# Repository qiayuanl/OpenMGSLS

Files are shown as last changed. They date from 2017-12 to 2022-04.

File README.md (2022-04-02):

# OpenMGSLS
**This project was developed in high school, is very naive and low reference value, please refer to it with caution!**

A brief Introduction and demo video show in [my webstie](https://qiayuanliao.netlify.app/project/sls/) 

## Introduction
There have many 3D printing technologies, many of them use the laser to process materials like SLS(Selective Laser Sintering). Move the laser quickly and accurately became an important thing in the 3D printing. Laser galvanometer which widely used in industrial marking has the many advan- tages such as high-speed and high-precision.So this project tries to develop a system which can use laser galvanometer in 3D printing.
## methord
Laser galvanometer works the same as the voltmeter, the volt determines the angle of mirrors which reflect the laser. We use serial to communicate with the computer and receive the GCode(GCode is most widely used nu- merical control programming language), process the GCode and plan, cal- culate the mirrors angle for each movement, use SPI to send the volt data to the DAC module, output the volt and make galvanometer turn to the corresponding angle.Then this poject develop a desktop SLS 3D printer to test the control system.
## date
The galvanometer control system and 3D printer developed in this project are compatible with most 3D printing slicing software(like simplify3D Cura), the laser point movement speed can reach 2,000mm/s, the print accuracy can reach 0.01mm and it can print many complex structures without sup- ports.
## summary
This project develops a system which can use the GCode to control the galvanometer and build a desktop SLS 3D printer base on this system. Rely on this system the printer can do 3D printing faster and more accurately than most of another desktop 3D printer.

## 引言
现存的 3D 打印技术中许多使用激光来加工材料，快速且精确地移动激光非常重要。激光振镜广泛应用于工业打标，具有高速、高精度的优点。本项 目是开发了一套可以在选择性激光烧结 3D 打印机上使用激光振镜的系统。

## 方法
激光振镜的工作原理与电压表相同，电压决定偏转激光的反射镜的角度。 这个项目使用串又与计算机通讯并接收 G代码(G 代码是使用最广泛的数 控编程语言)，对其进行处理规划，计算每个运动对应的电压，使用SPI将数据输出到DAC模块，输出电压，使振镜转到相应的角度。后另外开发了一台选择性激光烧结3D打印机来实验开发的控制系统。

## 数据
这个项目开发的振镜控制系统及3D打印机可以兼容大多数3D打印切片软件如:Simplify3D、Cura。激光点移动速度可以达到 2,000mm/s，打印精度可以达到0.01mm。

## 总结
这个项目开发了一个可以使用 GCode 来控制振镜的系统, 并在此基础上开发了一台桌面级选择性激光烧结3D打印机，可以比其他大多数桌面3D打印机更快，更准确地进行 3D 打印。



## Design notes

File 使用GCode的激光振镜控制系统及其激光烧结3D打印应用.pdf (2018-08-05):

# 使⽤ GCode 的激光振镜控制系统及其激光烧 结 3D 打印应⽤

### 廖洽源

⾼三级

### 潮州市⾦⼭中学 March 27, 2018

Abstract

现存的 3D 打印技术中许多使⽤激光来加⼯材料，快速且精确地移动激 光⾮常重要。激光振镜⼴泛应⽤于⼯业打标，具有⾼速、⾼精度的优点。本项 ⽬是开发了⼀套可以在选择性激光烧结 3D 打印机上使⽤激光振镜的系统。 激光振镜的⼯作原理与电压表相同，电压决定偏转激光的反射镜的⾓度。 这个项⽬使⽤串⼜与计算机通讯并接收 G 代码（G 代码是使⽤最⼴泛的数 控编程语⾔），对其进⾏处理规划，计算每个运动对应的电压，使⽤ SPI 将 数据输出到 DAC 模块，输出电压，使振镜转到相应的⾓度。后另外开发了 ⼀台选择性激光烧结 3D 打印机来实验开发的控制系统。 这个项⽬开发的振镜控制系统及 3D 打印机可以兼容⼤多数 3D 打印切 ⽚软件如：Simplify3D、Cura。激光点移动速度可以达到 2,000mm/s，打印 精度可以达到 0.01mm。
这个项⽬开发了⼀个可以使⽤ GCode 来控制振镜的系统，并在此基础上 开发了⼀台桌⾯级选择性激光烧结 3D 打印机，可以⽐其他⼤多数桌⾯ 3D 打印机更快，更准确地进⾏ 3D 打印。

There have many 3D printing technologies, many of them use the laser to process materials like SLS(Selective Laser Sintering). Move the laser quickly and accurately became an important thing in the 3D printing. Laser galvanometer which widely used in industrial marking has the many advantages such as high-speed and high-precision.So this project tries to develop a system which can use laser galvanometer in 3D printing.
Laser galvanometer works the same as the voltmeter, the volt determines the angle of mirrors which reflect the laser. We use serial to communicate with the computer and receive the GCode(GCode is most widely used numerical control programming language), process the GCode and plan, calculate the mirrors angle for each movement, use SPI to send the volt data to the DAC module, output the volt and make galvanometer turn to the corresponding angle.Then this poject develop a desktop SLS 3D printer to test the control system.
The galvanometer control system and 3D printer developed in this project are compatible with most 3D printing slicing software(like simplify3D Cura), the laser point movement speed can reach 2,000mm/s, the print accuracy can reach 0.01mm and it can print many complex structures without supports.
This project develops a system which can use the GCode to control the galvanometer and build a desktop SLS 3D printer base on this system. Rely on this system the printer can do 3D printing faster and more accurately than most of another desktop 3D printer.

2

## Contents

1 前言 | 4
2 控制理论及实现 | 7
3 机械设计 | 10
4 结果 | 12
5 结论 | 13
6 致谢 | 13
7 参考文献 | 13

3

## 1 前言

### 1.1 激光打标

激光打标是使⽤激光束在各种不同的
物质表⾯打上永久的标记的过程的统称, 电
⼦元器件、集成电路 (IC)、五⾦制品等都
是⽤这种设备来为产品加上商标 (⼆维⽮
量图).

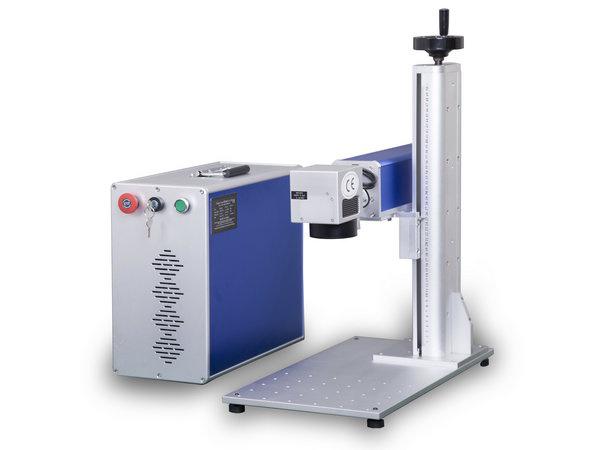
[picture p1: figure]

(a) 常见激光打标机

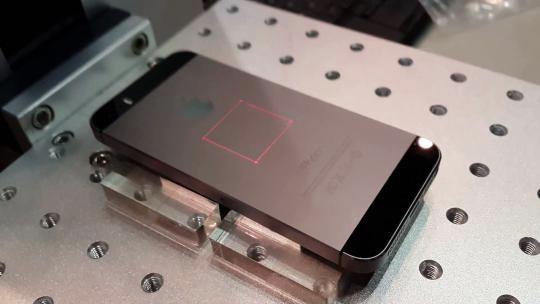
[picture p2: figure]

(b) iPhone ⼿机背⾯⽂字商标为激光打标制造

Figure 1: 激光打标

### 1.1.1 振镜电机

振镜是⼀种优良的⽮量扫描器件. 它是
⼀种特殊的摆动电机, 基本原理是通电线
圈在磁场中产⽣⼒矩, 但与旋转电机不同,
其转⼦上通过机械纽簧或电⼦的⽅法加有
复位⼒矩, ⼤⼩与转⼦偏离平衡位置的⾓
度成正⽐, 当线圈通以⼀定的电流⽽转⼦
发⽣偏转到⼀定的⾓度时, 电磁⼒矩与回
复⼒矩⼤⼩相等, 故不能象普通电机⼀样
旋转, 只能偏转, 偏转⾓与电流成正⽐, 与
电流计的原理相同, 故振镜又叫电流计扫
描器 (galvanometric scanner).

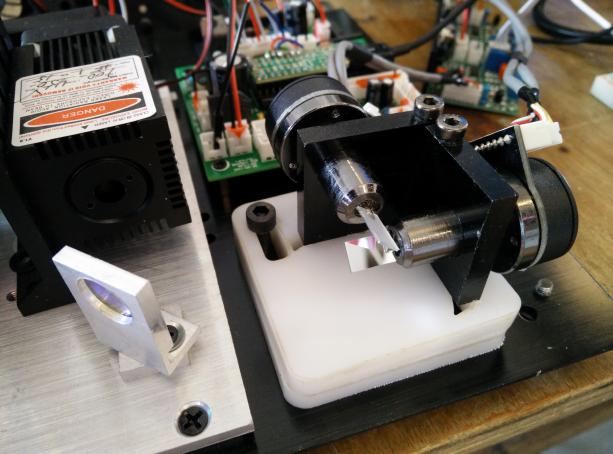
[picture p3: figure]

Figure 2: 两个振镜电机和激光器构成的
XY ⼆维扫描系统

### 1.2 3D 打印

3D 打印机又称三维打印机 (3DP), 是
⼀种累积制造技术, 即快速成形技术的⼀
种机器, 它是⼀种数字模型⽂件为基础, 运
⽤特殊蜡材、粉末状⾦属或塑料等可粘合
材料, 通过打印⼀层层的粘合材料来制造
三维的物体. 现阶段三维打印机被⽤来制
造产品. 3D 打印⽆需机械加⼯或模具, 就
能直接从计算机图形数据中⽣成任何形状
的物体, 从⽽极⼤地缩短了产品的⽣产周
期, 提⾼了⽣产率, 在⼯业 (制造业、航天科
技、医疗⾏业等) 及民⽤ (教育研究、⽣活
⽤品等) 领域有着许多应⽤.

1.2.1 3D 打印机原理概述

3D 打印的⼀般流程如下:

建模 3D 打印模型可以使⽤计算机辅助设
计软件 (SolidWorks、AutoCAD) 或三维扫 描仪⽣成. ⼿动搜集制作 3D 图像所需的⼏
何数据过程同雕塑等造型艺术类似. 通过
3D 扫描, 可以⽣成关于真实物体的形状、外
表等的电⼦数据并进⾏分析. 以 3D 扫描得
到的数据为基础, 就可以⽣成被扫描物体
的三维电脑模型. ⽆论使⽤哪种 3D 建模软
件, ⽣成的 3D 模型 (通常为.skp、.dae、.3ds 或其它格式) 都需要转换成.STL 或.OBJ 这
类以三⾓形作为 3D 模型的基本单元的格
式.

分层 把模型放在 XY 平⾯上,Z 轴对应的
就是模型⾼度. 把 XY 平⾯抬⾼⼀定⾼度
再与模型的表⾯相交, 就可以得到模型在
这个⾼度上层切⽚. 所谓的分层就是每隔
⼀定⾼度就⽤⼀个 XY 平⾯去和模型相交
作层切⽚, 全部切完后就可以得到模型在
每⼀个⾼度上的轮廓线. 分层本质上就是
⼀个把 3D 模型转化为⼀系列 2D 平⾯的
过程, ⾃此之后的所有操作就都是在 2D 图
形的基础上进⾏. 将 XY 平⾯与构成模型
的三⾓⾯进⾏相交, ⼀个平⾯和⼀个三⾓
形相交, 就得到⼀条线段. 将这些线段连起
来就能得到某 Z 轴⾼度的 XY 轴外形轮廓.
改变 z 轴⾼度便能得到不同层的外形轮廓.

路径及 GCode 生成 得到外形轮廓后通
过算法⽣成填充路径后将路径转换成数控
程序 (铣床车床钻床等) 通⽤的 G 代码.

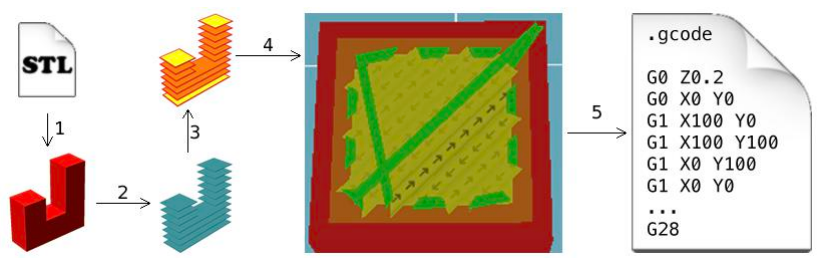
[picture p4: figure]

Figure 3: 电脑上的处理过程

### 1.2.2 常见 3D 打印机成型原理细分

在 20 世纪 70 年代后期, 出现了许多不
同的 3D 打印⽅法, 主要有三种熔融沉积成
型 (FDM)、⽴体光刻技术 (SLA)、选择性
激光烧结术 (SLS)

熔融沉积成型 (Fused deposition modeling, FDM) 是⼀种将各种热熔性的丝状
材料 (ABS 和 PLA 等) 加热熔化成形的⽅
法. 又可被称为 FFM 熔丝成型 (Fused Filament Modeling) 或 FFF 熔丝制造 (Fused Filament Fabrication), 其后两个不同名词 主要只是为了避开前者 FDM 专利问题,
然⽽核⼼技术原理与应⽤其实均是相同的.
材料被加热到半液体状态后, 在 GCode 的
控制下,FDM 装置的喷嘴就会沿着模型图
的表⾯移动, 将热塑性材料挤压出来, 在
该层中凝固形成轮廓.FDM 装置会使⽤两
种材料来执⾏打印的⼯作, 分别是⽤于构
成成品的建模材料和⽤作⽀架的⽀撑材料,

透过喷嘴垂直升降, 材料层层堆积凝固后,
就能由下⽽上形成⼀个 3D 打印模型的实
体. 打印完成实体.
(a) 1 为喷头 2 为打印半完成的零件 3 为底板

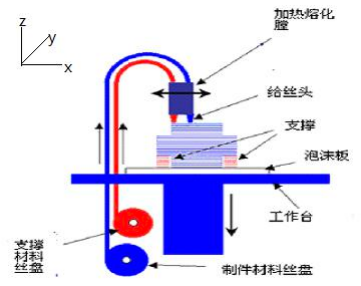
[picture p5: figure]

(b) 另⼀个视⾓

Figure 4: FDM3D 打印原理

优点 在 3D 打印技术中,FDM 的机械
结构最简单, 设计也最容易, 制造成本、维
护成本和材料成本也最低, 因此桌⾯级 3D
打印机中⼤部分使⽤的是这种技术.

缺点 难以精确控制出料形态与成型
效果, 同时温度对于 FDM 成型效果影响
⾮常⼤, ⽽桌⾯级 FDM 3D 打印机通常
都缺乏恒温设备, 因此基于 FDM 的桌⾯
级 3D 打印机的成品精度通常为 0.3mm-0.2mm 成品效果依然不够稳定, 在打印悬
空结构时还必须从⼀开始便构建“⽀撑”, 导
致精度进⼀步降低. 此外, 所以在对精度要
求较⾼的快速成型领域较少采⽤ FDM.

(a) 不打印⽀撑时对模型的要求

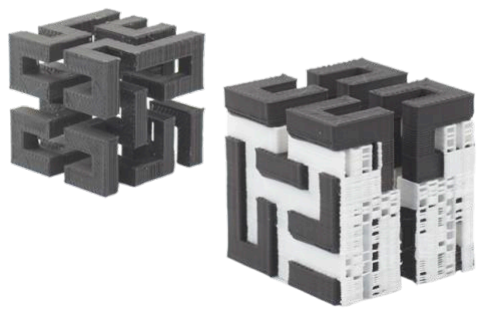
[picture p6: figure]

(b) ⽀撑去除前后对⽐ (⽩⾊为⽀撑)

Figure 5: FDM 对于零件的要求

选择性激光烧结 (Selective Laser Sintering,SLS) 选择性激光烧结使⽤激光将
粉末材料层熔化和固化成成品, 当激光打
到粉末上, 粉末会融化并且和附近粉末粘
在⼀起, 当激光在粉末层上匀速扫过⼀条
直线时, 粉末便会固化成⼀条细丝, 激光不
断扫描出⾯时, 粉末便可以被固化成⾯, 在
形成的⾯上⾯再铺⼀层粉末, 激光继续扫
描, 不断重复这个过程, 就能得到⼀个 3D
零件.

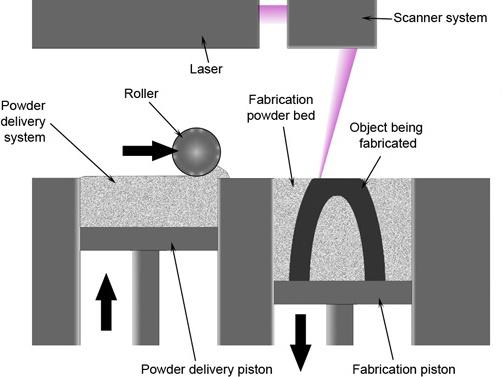
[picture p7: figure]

Figure 6: SLS3D 打印原理

优点 SLS 主要⽤于⼯业 3D 打印应⽤,
激光烧结技术可以使⽤⾮常多的粉末材料,
并制成相应材质的成品 SLS ⼴泛⽤于⽣产
功能原型和零件以及⼀些最终产品. 激光
烧结的最⼤优点是⼏乎完全的设计⾃由度;
过量的未熔化粉末在其⽣产时⽤作结构的
⽀撑, 这允许制造复杂的结构, ⽽不需要像
FDM SLA DLP 等构建额外的⽀撑.

缺点 技术⼗分复杂, 需要较⼤功率激
光, 桌⾯级的 SLS3D 打印机只少量存在于
⾼校或团队.

### 1.3 同类项目

### 1.3.1 现存桌面级 SLS3D 打印机

现存的桌⾯级 SLS3D 打印机都是在 FDM
3D 打印机 (或者激光切割机) 基础上改装
⽽成,XY 轴都是使⽤步进电机 + 同步带或
丝杠的⽅式拖着激光器进⾏直线运动, 这
种机构的最⼤运动速度只能到达 200mm/s
左右.

OpenSLS 项目 由美国莱斯⼤学约旦⽶
勒⽣理系统和先进材料实验室开发. 这个
项⽬的研究的主要⽅向为粉末烧结材料, 是
⽤⼀台 CO2 切割机改装⽽成.

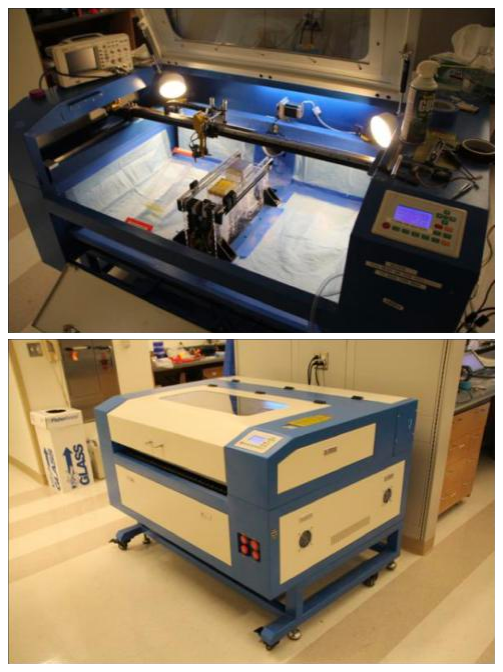
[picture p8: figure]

Figure 7: OpenSLS

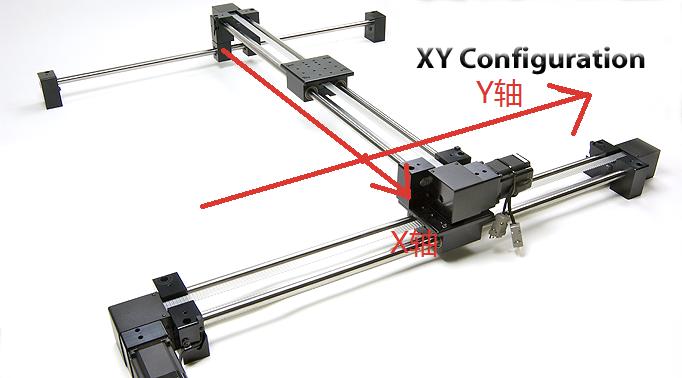
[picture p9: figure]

Figure 8: 步进电机直线模组

### 1.4 本项目简介

选题动机 步进电机直线模组的最⼤运动
速度只能到达 200mm/s 左右, 换⾔之, 激光 光斑的移动速度最⼤只有 200mm/s, ⽽激
光打标机的振镜电机进⾏扫描速度能达到
1000mms-5000mm/s, 是步进电机直线模组 的⼏⼗倍, 为什么不把激光打标机的执⾏
器 (两个振镜组成的振镜组) ⽤在 SLS3D
打印机上⾯??? 激光打标机使⽤的是⼆维
⽮量图不能适⽤于于 3D 打印, 所以开发⼀
个使⽤ Gcode 控制的振镜扫描系统是最佳
的选择.

目标 开发⼀个运⾏在 Arduino Due 单⽚
机上的控制程序及配套硬件, 可以⽤数控
设备通⽤的 G 代码控制振镜, 使得振镜兼
容常规切⽚软件, 可以⽤于 SLS3D 打印, 并
在此基础上研制使⽤振镜电机作为 XY 轴
的桌⾯级 SLS3D 打印机.

实现方法 在 PC 上使⽤切⽚软件将 3D
模型转换成 GCode, 每⾏ GCode 包含了
运动轨迹的信息, 将 GCode 通过串⼜发
送到 Arduino 控制器上,Arduino 控制器对 GCode 进⾏解释, 判断是否需要进⾏烧结
和移动粉缸和改变预热温度的操作及操作
数值, 对其进⾏进⼀步规划后执⾏, 后对
PC 进⾏应答⽽获取下⼀⾏ GCode, 不断
执⾏直⾄打印完成.

## 2 控制理论及实现

本章介绍本项⽬中振镜电机的控制及
补偿算法和步进电机加速度算法.

### 2.1 振镜扫描控制

### 2.1.1 单轴振镜电机直线扫描控制

条件 设⼀垂直于振镜旋转轴的直线及原
点, 反射镜⾯与直线夹⾓ π
4

, 运动⽬标点坐
标 x, 振镜中⼼与原点距离 d 且在原点正上
⽅, 反射镜偏⾓ α

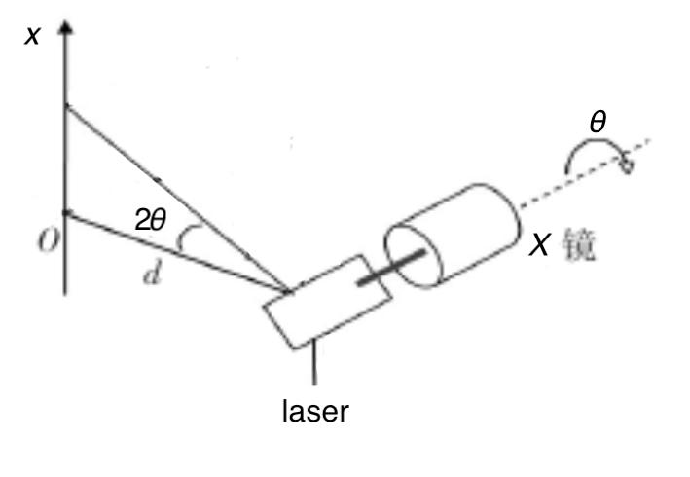
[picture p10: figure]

Figure 9: 单轴振镜电机⽰意图

正运动学:

x = d tan 2α | (1)

逆运动学:

α =

1
2

arctan

x
d

(2)

控制要求

输入: 运动⽬标点坐标 x

输出: 反射镜偏⾓ θ

控制函数 即逆运动学

f(x) = θ =

1
2

arctan

x
d

(3)

### 2.1.2 双轴振镜电机组平面扫描控制

条件 如果简单地使⽤单轴振镜电机的控
制⽅法

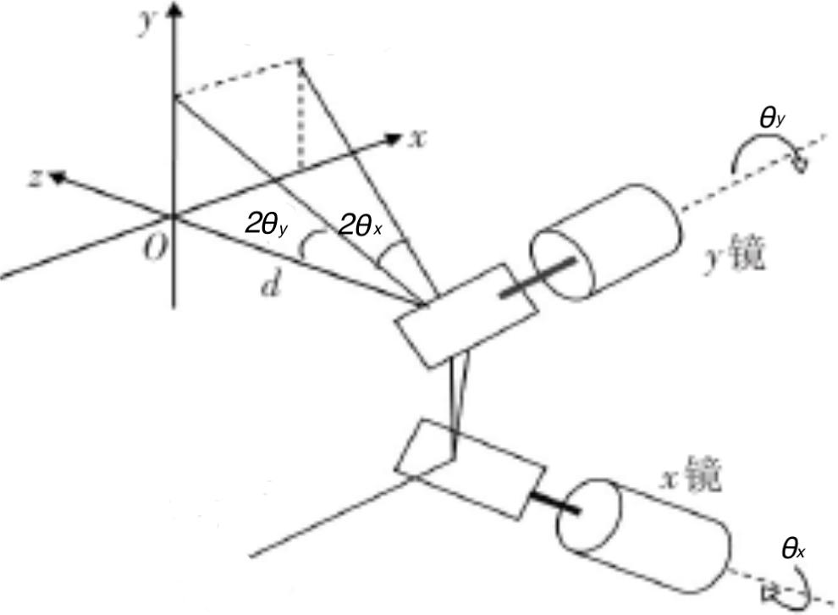
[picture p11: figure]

Figure 10: 双轴振镜电机组⽰意图

正运动学:
{
x = d tan 2θx
y = d tan 2θy

(4)

逆运动学:
{
2θx = arctan x
d
2θy = arctan y
d

(5)

控制要求

输入: 运动⽬标点坐标 (x, y)

输出: x 轴振镜反射镜偏⾓ θx , y 轴振
镜反射镜偏⾓ θy

控制函数
f(x, y) = {
θx =

1/2 arctan x
d
θy =

1/2 arctan y
d

(6)

但是如果使⽤这种控制⽅式,y 轴将会产⽣
枕型失真.

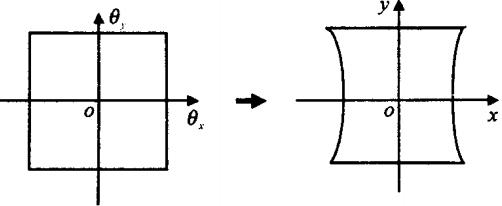
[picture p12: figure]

Figure 11: 扫描正⽅形图形的枕型失真

使⽤上述控制⽅式控制双轴的振镜组,
没有考虑到两个振镜的距离

条件 设 x 振镜和 y 振镜反射镜中轴之间
的距离为 e,y 振镜的轴线到扫描平⾯坐标
原点的距离为 d, 当 x,y 轴的光学偏转⾓分
别为 θx 和 θy 时, 扫描平⾯上相应激光斑坐
标为 (x, y), 当 θx = θy = 0 时,

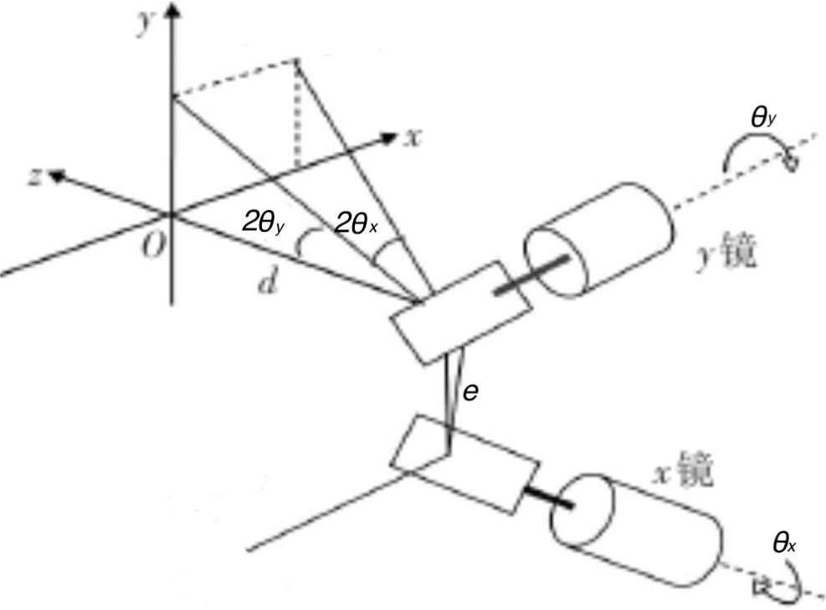
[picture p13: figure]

Figure 12: 双轴振镜电机组⽰意图

正运动学:
{
x = (e +

√
d

2 + y

2

)tan 2θx
y = d tan 2θy

(7)

逆运动学:

2θx = arctan x
e+

√
| d

2+y

2
2θy = arctan y
d

(8)

可见, 双轴振镜组的运动学模型是复杂的
⾮线性模型.

### 2.1.3 双轴振镜电机失真分析

失真产生 使⽤单轴扫描⽅式控制双轴振
镜组扫描垂直于 x 轴的直线时,θx 不变, 设
常数 c = 2 tan θx 由 (7) 可得

(x − ce)

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
= 1 | (9)

显然 (9) 描述的曲线为双曲线
定义 ε 为误差 x0 为预期位置 x 为实际位
置, 可见当 e 和 x0 越⼤时,x 轴偏移 ε 将越 ⼤

ε = x − x0 = (e +

√
d

2 + e

2

)tan 2θx (10)

验证 使⽤ Matlab 软件仿真扫描, 当 e = 5mm,d = 200mm 扫描长宽为 50mm 的正
⽅形图案

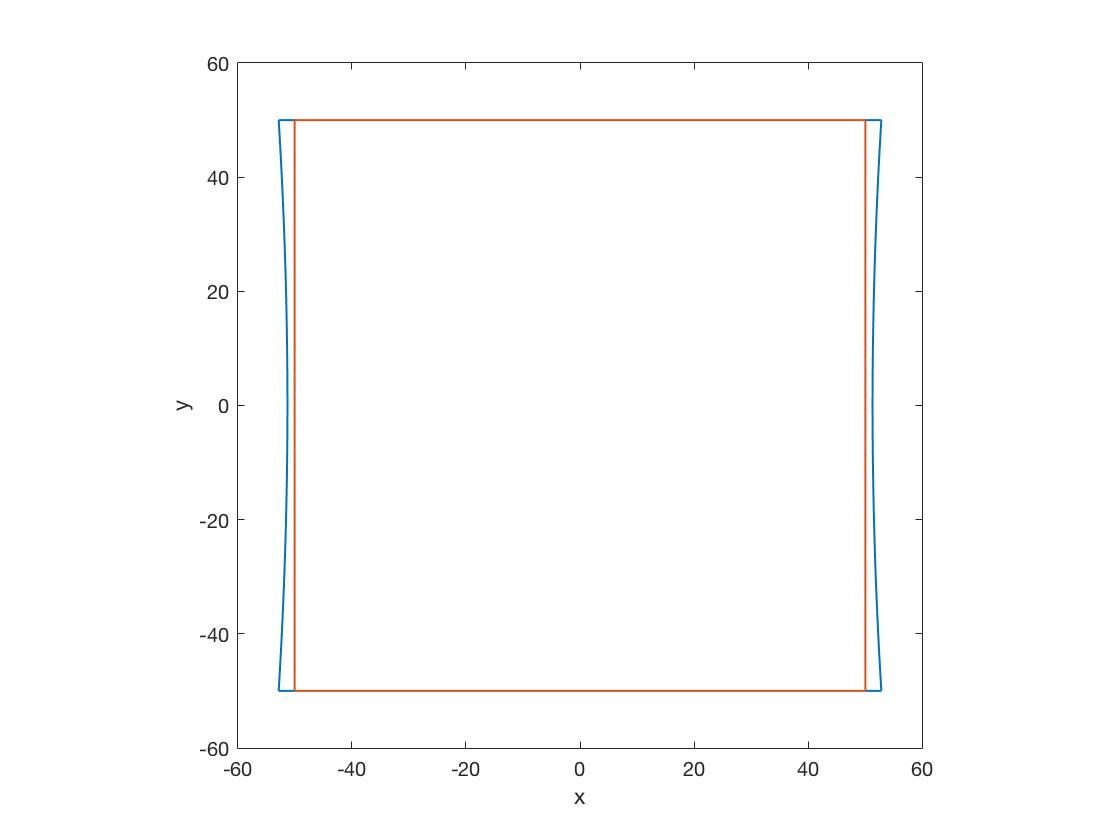
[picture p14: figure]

Figure 13: Matlab 仿真结果, 橙⾊为预期 图形, 蓝⾊为实际扫描图形

### 2.1.4 振镜控制实现

解释从串⼜接收的 G 代码缓存到队列
中, 空闲时间对其进⾏解析, 根据依据设

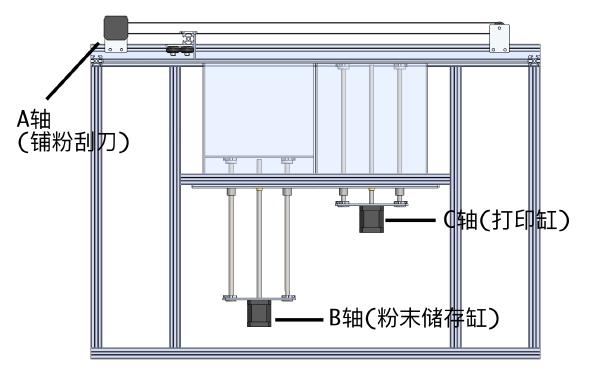
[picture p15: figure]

置的每秒插补次数对运动的路径进⾏分割，
对每个插补的 XY 轴分别计算⾓度, 后转换
成 DA 数值, 储存在两个队列中, 最后使⽤
定时器让振镜在某个细分时间点 pop 出队
列中的 DA 值, 通过 SPI 总线与 DAC8852(双 路) 以 50M 的速度进⾏通信, 将 DA 值
(DAC8552 为 16 位 0-5V 对应 0-65536) 发 送给 DAC 模块.

### 2.2 步进电机控制理论及实现

对于 SLS3D 打印机来说, ⼀共需要控
制 3 个轴:A 轴 (铺份刮⼑),B 轴 (粉末储存 缸),C 轴 (打印缸) 来完成铺粉过程
通过脉冲控制步进电机, 脉冲间隔决定电
机旋转速度, 需要考虑电机的加减速, 否则
电机将很容易失步

Figure 14: 三个直线运动轴

### 2.2.1 单轴步进电机加减速控制

条件 S 为加速距离 (单位:step), a 为加速 度 (单位:step/s
2

), v0 为初始速度 (单位:step/s),
v 为⽬标速度 (单位:step/s), t 为加速度时 间 (单位:s)

运动学

s =

v

2 − v

2
0
2a

(11)

v =

√
v

2
0 + 2aS | (12)

设 i 为第⼏步

vi =

√
v

2
i−1 + 2a | (13)

控制 使⽤定时器控制脉冲发送间隔设: Pi
为第 i 步的间隔时间 (单位:ticks) F 为定 时器唤醒周期 (单位 ticks/s)
Pi = F/vi | (14)

由 (13) 和 (14) 得:

Pi =

F
√

F
Pi−1

2
+ 2a

(15)

即

Pi =

Pi−1
√
1 + P

2
i−1

2a
F²

(16)

化简 泰勒展开在 −1 ≤ n ≤ 1 时
√

1
1+n ≈ 1 −

n

2 所以

Pi = Pi−1(1 −

P

2
i−1a
F²

) (17)

⽽ a F² 为常数

### 2.2.2 步进电机控制实现

在 (17) 中, ⽽ a F² 在加速度不变时为
常量, 在程序编译或者控制板开启时可以
预先计算在后⾯的运算中作为常量乘⼦参
与运算
设 R =
a

F² 则有
初始化:

P =

F
√
V

2
0 + 2a

(18)

加速时:
P = P(1 − RP²
) | (19)
到达⽬标速度时:
P = P | (20)

减速时:
P = P(1 + RP²
) | (21)
除了初始化, 其他计算只有乘法和加法, 因
此效率很⾼.
在控制板开启时初始化, 计算出第⼀次的
脉冲时间间隔, 设定定时器, 每次被定时器
唤醒就发送⼀个脉冲并计算下⼀个脉冲间
隔时间, 并根据计算出来的脉冲设定定时
器的唤醒间隔.

## 3 机械设计

本章介绍 SLS3D 打印机的机械结构都
使⽤ Solidworks 建模装配
⼀共开发了三代原型机, ⼀个实验平台, 将
着重介绍第三代. 细节详见公开的 solidworks 源⽂件

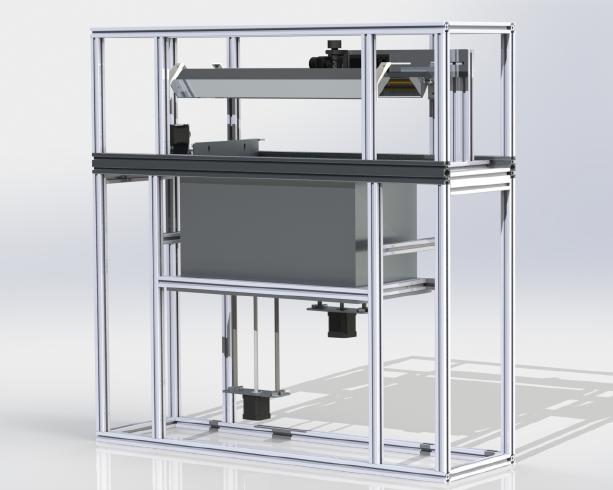
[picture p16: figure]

Figure 15: 第三代打印机渲染图

### 3.1 前代打印机

第一代 40WCO2 激光管激光振镜亚克⼒
及铝型材搭建的 Z 轴此版本的因为设计时
没有考虑到 CO2 激光功率过⼤，需要⽔冷，
亚克⼒不耐热等问题⽆法使⽤.

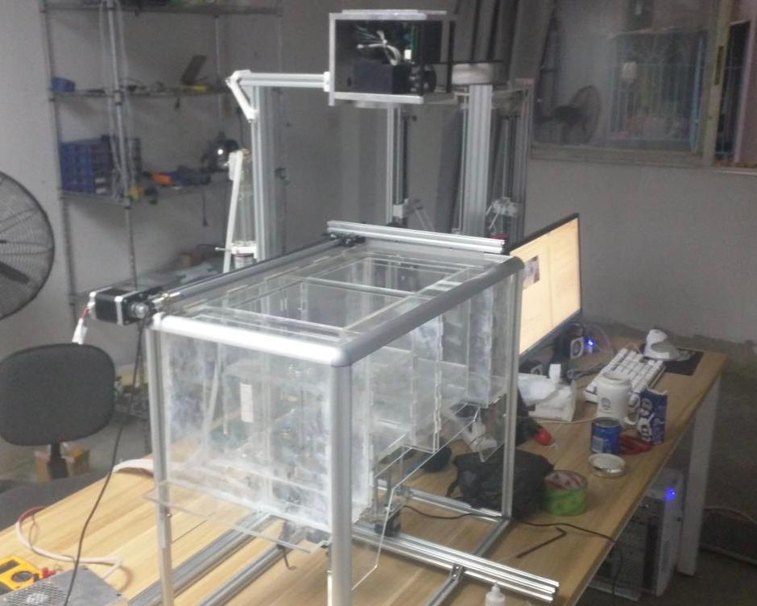
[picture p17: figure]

Figure 16: 第⼀代打印机实物图

第二代 使⽤半导体激光激光振镜铝板铝
型材搭建的第⼆代原型机

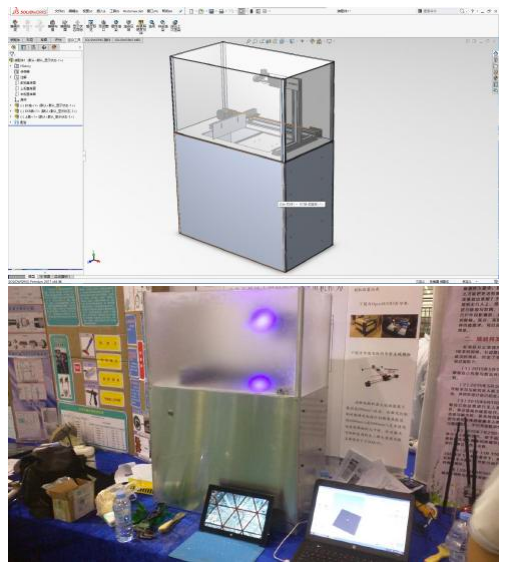
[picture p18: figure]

Figure 17: 第⼆代打印机渲染图及实物图

### 3.2 二维烧结实验平台

⼆维烧结实验平台⽤于单层烧结实验,
使⽤ 5W 半导体激光 (450nm) 及激光振镜, 并在底部加装加热板对粉末预热

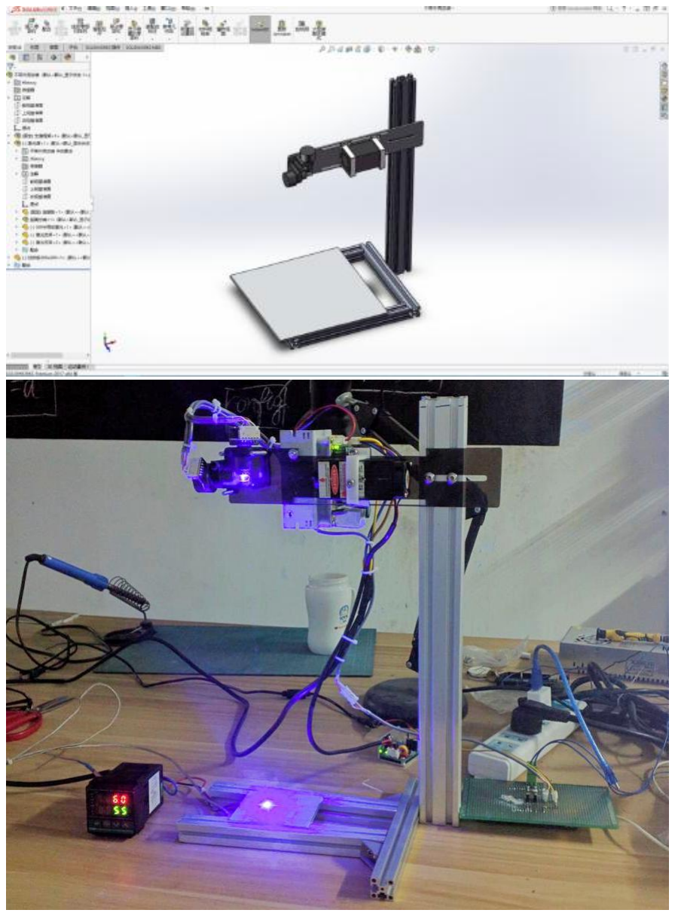
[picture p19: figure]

Figure 18: ⼆维烧结实验平台模型图及实
物图

### 3.3 第三代 SLS 打印机

打印机由三部分构成:
激光机构 (XY 轴)
粉末机构 (ABC 轴)
加热机构

激光机构 激光机构由两个振镜电机依照
上章所述的⽅式安装, 使⽤了⼀个 5W450nm
半导体激光器.

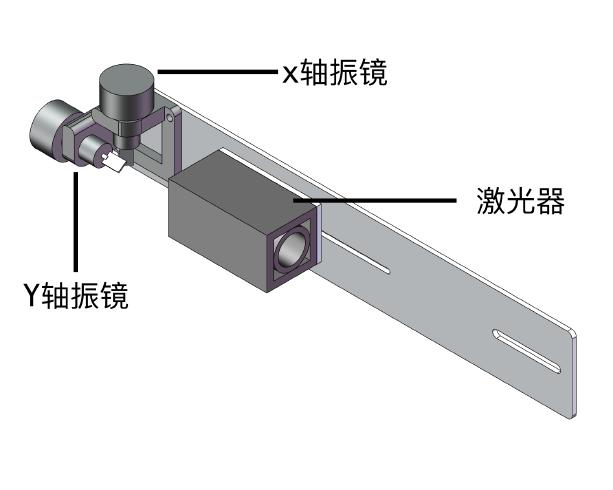
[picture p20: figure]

Figure 19: 激光机构

粉末机构 粉末机构的作⽤是覆盖⼀层粉
末到已烧结完成的打印件上⾯, 从⽽完成
整个三维堆积的过程
具体的过程如下:
初始状态时, 粉末储存缸 (B 轴) 的推杆降
到最低, ⽽打印缸推杆 (C 轴) 上升到距离
缸⼜极⼩的距离, 将两个缸都装满粉, 刮⼑
往返运动⼀次, 这时打印缸内便有了⼀层
薄⽽又均匀的粉末, 进⾏平⾯烧结后, 打印
缸下降⼀段距离, 粉末储存缸上升⼀段距
离, 这时便有部分粉末从粉末储存缸的缸
⼜溢出, 刮⼑往返⼀次, 将粉末储存缸的粉
末带到打印缸, 并铺匀, 这时, 第⼀次平⾯
烧结得到的打印件上⾯便覆盖了⼀层粉末,
继续扫描, 扑粉, 不断重复这个过程.

Figure 20: 粉末机构

加热机构 使⽤两个红外加热管对粉末进
⾏预热

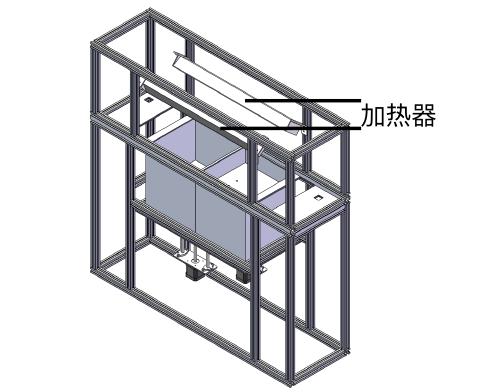
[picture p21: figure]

Figure 21: 加热机构

整机 整机模型图

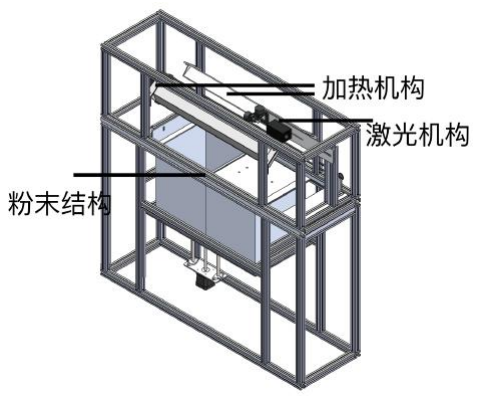
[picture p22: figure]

Figure 22: 整机

## 4 结果

单层烧结

扫描性能 在不考虑激光功率的情况
下, 振镜电机在 GCode 的控制下速度可以
达到 1000mm/s ⾄ 5000mm/s, 速度越快, 精度越低.

烧结结果 使⽤ XY 测试平台使⽤⿊⾊
碳粉末和⽩⾊ PLA 粉末混合, 增加激光被
吸收的热量, 进⾏单层烧结实验, 可以得到
精密结合的薄塑料⽚.

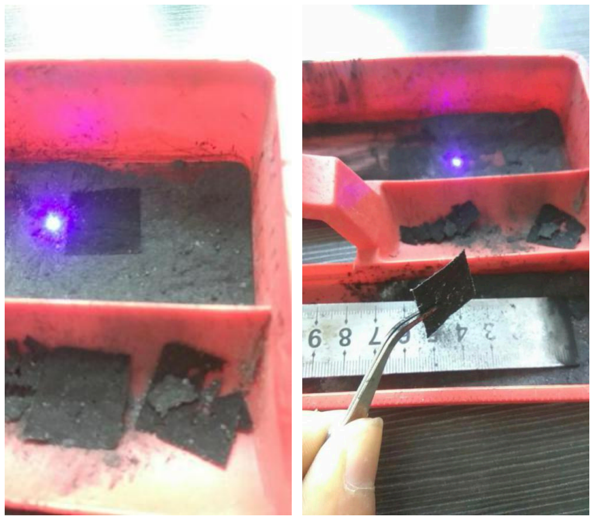
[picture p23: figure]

Figure 23: 单层烧结

多层烧结 (即 3D 打印) 使⽤第三代打印
机对粉末进⾏进⾏多层烧结, 层与层之间
粘黏良好, 可以打印出许多结构及其复杂
(其他打印机难以打印出来) 的模型.

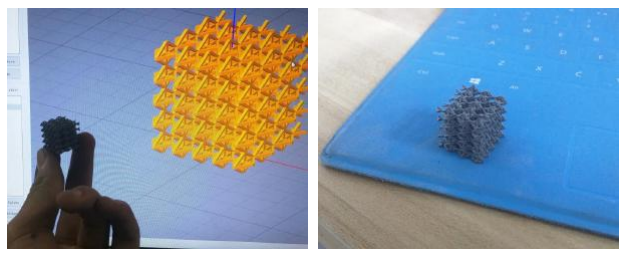
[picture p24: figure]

Figure 24: 多层烧结 (3D 打印)

## 5 结论

本项⽬成功开发⼀个运⾏在 Arduino Due
单⽚机上的控制系统, 可以⽤数控设备通
⽤的 G 代码控制振镜, 使得振镜电机组兼
容常规 3D 切⽚软件, 可以⽤于 SLS3D 打
印, 并在此基础上开发使⽤振镜电机作为
XY 轴的桌⾯级 SLS3D 打印机, 并使⽤开
发的出来的 SLS3D 打印机成功打印出塑料
打印件
作为⼀个系统, 在根据不同材料要求更换
激光器的功率波长后, 理论上可以兼容其
他材料, 如⾦属, 铸造蜡, 光敏树脂等.

## 6 致谢

在项⽬的研究过程中, 潮州市⾦⼭中学、
潮州市科学技术协会、指导⽼师黄胜刚给
了我很⼤的帮助.

## 7 参考文献

赵毅, 卢秉恒. 振镜扫描系统的枕形畸
变校正算法 [J]. 中国激光, 2003, 30(3): 216-218.
Eiderman A. Real Time Stepper Motor Linear Ramping Just by Addition and Multiplication[J].
Margolis, Michael. Arduino Cookbook: Recipes to Begin, Expand, and Enhance Your Projects. ” O’Reilly Media, Inc.”, 2011.

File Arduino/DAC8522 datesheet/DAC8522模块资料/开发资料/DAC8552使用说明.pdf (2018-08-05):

## 梦想电子工作室


联系方式：http://mcu-dream.taobao.com

# DAC8552 使用说明

一：模块介绍

DAC8552 模块为 16 位双路 DA。

使用 DAC8552+ REF02（贴在板子背面）

二：接线图

三：接线说明

1、VIN 端口：8~40V（或 2.7~5.5V）

2、DIN、SCLK、SYNC 端口：SPI 协议接口

3、A、B 端口：模拟电压输出通道

4、+5V 端口：由 REF02 产生，不需要外部输入

注：背面焊接 REF02：VIN 输入 8~40V，+5V 不输入

不焊接 REF02：+5V 输入 2.7~5.5V，VIN 不输入

此时参考电压和输入电压一致

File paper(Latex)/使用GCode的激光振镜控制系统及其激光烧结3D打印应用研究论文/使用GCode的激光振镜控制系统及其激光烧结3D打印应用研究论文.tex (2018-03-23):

\documentclass[a4paper,12pt,onecolumn,twoside]{article}
%%package
\usepackage[UTF8, heading = false, scheme = plain]{ctex} %中文支持
\usepackage{fancyhdr}
\usepackage{indentfirst} % 中文段落首行缩进
\usepackage{bm}          % 公式中的粗体字符(用命令\boldsymbol)
\usepackage{multicol}    % 正文双栏
\usepackage{indentfirst} % 中文首段缩进
\usepackage{graphicx} 
\usepackage{geometry}
\usepackage{caption}
\usepackage{subfigure} %子图片

\usepackage{tikz}%流程图
\usetikzlibrary{shapes,arrows,chains}%
\usepackage{xcolor}%
 
%%title

\title{使用GCode的激光振镜控制系统及其激光烧结3D打印应用}
\date{}
\begin{document}
\maketitle
\vspace{5in}
\begin{flushright}
\large{
	廖洽源\\
	高三级\\
	潮州市金山中学\\
	\today
}
\end{flushright}

\thispagestyle{empty} 　　　%首頁頁碼空白
%%content
\tableofcontents
\newpage
\newgeometry{left=1in,right=1in,top=1in,bottom=1in} %更改边距

\twocolumn
%前言
\section{前言}
\subsection{激光打标}
激光打标是使用激光束在各种不同的物质表面打上永久的标记的过程的统称,电子元器件、集成电路(IC)、五金制品等都是用这种设备来为产品加上商标(二维矢量图).
\begin{figure}[ht]
\centering
\subfigure[常见激光打标机]{ 
\centering

}
\subfigure[iPhone手机背面文字商标为激光打标制造]{
\centering     

}
\caption{激光打标}
\end{figure}
\subsubsection{振镜电机}
振镜是一种优良的矢量扫描器件.它是一 种特殊的摆动电机,基本原理是通电线圈在磁场中 产生力矩 ,但与旋转电机不同,其转子上通过机械纽 簧或电子的方法加有复位力矩 ,大小与转子偏离平 衡位置的角度成正比 ,当线圈通以一定的电流而转子发生偏转到一定的角度时 ,电磁力矩与回复力矩大小相等 ,故不能象普通电机一样旋转 ,只能偏转,偏转角与电流成正比 ,与电流计的原理相同 ,故振镜又叫电流计扫描器(galvanometric scanner).
\begin{figure}[ht]
\centering

\caption{两个振镜电机和激光器构成的XY二维扫描系统}
\end{figure}

\subsection{3D打印}
3D打印机又称三维打印机(3DP),是一种累积制造技术,即快速成形技术的一种机器,它是一种数字模型文件为基础,运用特殊蜡材、粉末状金属或塑料等可粘合材料,通过打印一层层的粘合材料来制造三维的物体.现阶段三维打印机被用来制造产品. 3D打印无需机械加工或模具,就能直接从计算机图形数据中生成任何形状的物体, 从而极大地缩短了产品的生产周期,提高了生产率,在工业(制造业、航天科技、医疗行业等)及民用(教育研究、生活用品等)领域有着许多应用.
\subsubsection{3D打印机原理概述}
3D打印的一般流程如下:
\paragraph{建模}
3D打印模型可以使用计算机辅助设计软件(SolidWorks、AutoCAD)或三维扫描仪生成.手动搜集制作3D图像所需的几何数据过程同雕塑等造型艺术类似.通过3D扫描,可以生成关于真实物体的形状、外表等的电子数据并进行分析.以3D扫描得到的数据为基础,就可以生成被扫描物体的三维电脑模型.
无论使用哪种3D建模软件,生成的3D模型(通常为.skp、.dae、.3ds或其它格式)都需要转换成.STL或.OBJ这类以三角形作为3D模型的基本单元的格式.
\paragraph{分层}
把模型放在XY平面上,Z轴对应的就是模型高度.把XY平面抬高一定高度再与模型的表面相交,就可以得到模型在这个高度上层切片.所谓的分层就是每隔一定高度就用一个XY平面去和模型相交作层切片,全部切完后就可以得到模型在每一个高度上的轮廓线.分层本质上就是一个把3D模型转化为一系列2D平面的过程,自此之后的所有操作就都是在2D图形的基础上进行.
将XY平面与构成模型的三角面进行相交,一个平面和一个三角形相交,就得到一条线段.将这些线段连起来 就能得到某Z轴高度的 XY轴外形轮廓.改变z轴高度便能得到不同层的外形轮廓.
\paragraph{路径及GCode生成}
得到外形轮廓后通过算法生成填充路径 后将路径转换成数控程序(铣床 车床 钻床等)通用的G代码.
\begin{figure}[ht]
\centering

\caption{电脑上的处理过程}
\end{figure}
\subsubsection{常见3D打印机成型原理细分}
在20世纪70年代后期,出现了许多不同的3D打印方法,主要有三种熔融沉积成型(FDM)、
立体光刻技术(SLA)、选择性激光烧结术(SLS)
\paragraph{熔融沉积成型(Fused deposition modeling, FDM)}
是一种将各种热熔性的丝状材料(ABS和PLA等)加热熔化成形的方法.又可被称为FFM 熔丝成型 (Fused Filament Modeling) 或FFF 熔丝制造 (Fused Filament Fabrication),其后两个不同名词主要只是为了避开前者FDM专利问题,然而核心技术原理与应用其实均是相同的.
材料被加热到半液体状态后,在GCode的控制下,FDM装置的喷嘴就会沿着模型图的表面移动,将热塑性材料挤压出来,在该层中凝固形成轮廓.FDM 装置会使用两种材料来执行打印的工作,分别是用于构成成品的建模材料和用作支架的支撑材料,透过喷嘴垂直升降,材料层层堆积凝固后,就能由下而上形成一个3D打印模型的实体.打印完成实体.
\begin{figure}[ht]
\centering
\subfigure[1为喷头 2为打印半完成的零件 3为底板]{
\centering     

}
\subfigure[另一个视角]{ 
\centering

}
\caption{FDM3D打印原理}
\end{figure}
\subparagraph{优点}
在3D打印技术中,FDM的机械结构最简单,设计也最容易,制造成本、维护成本和材料成本也最低,因此桌面级3D打印机中大部分使用的是这种技术.
\subparagraph{缺点}
难以精确控制出料形态与成型效果,同时温度对于FDM成型效果影响非常大,而桌面级FDM 3D打印机通常都缺乏恒温设备,因此基于FDM的桌面级3D打印机的成品精度通常为0.3mm-0.2mm成品效果依然不够稳定,在打印悬空结构时还必须从一开始便构建“支撑”,导致精度进一步降低.此外,所以在对精度要求较高的快速成型领域较少采用FDM.
\begin{figure}[ht]
\centering
\subfigure[不打印支撑时对模型的要求]{
\centering     

}
\subfigure[支撑去除前后对比(白色为支撑)]{ 
\centering

}
\caption{FDM对于零件的要求}
\end{figure}
\\
\paragraph{选择性激光烧结(Selective Laser Sintering,SLS)}
选择性激光烧结使用激光将粉末材料层熔化和固化成成品,当激光打到粉末上,粉末会融化并且和附近粉末粘在一起,当激光在粉末层上匀速扫过一条直线时,粉末便会固化成一条细丝,激光不断扫描出面时,粉末便可以被固化成面,在形成的面上面再铺一层粉末,激光继续扫描,不断重复这个过程,就能得到一个3D零件.
\begin{figure}[ht]
\centering     

\caption{SLS3D打印原理}
\end{figure}
\subparagraph{优点}
SLS主要用于工业3D打印应用,激光烧结技术可以使用非常多的粉末材料,并制成相应材质的成品SLS广泛用于生产功能原型和零件以及一些最终产品. 激光烧结的最大优点是几乎完全的设计自由度; 过量的未熔化粉末在其生产时用作结构的支撑,这允许制造复杂的结构,而不需要像FDM SLA DLP等构建额外的支撑.
\subparagraph{缺点}
技术十分复杂,需要较大功率激光,桌面级的SLS3D打印机只少量存在于高校或团队. 
\subsection{同类项目}
\subsubsection{现存桌面级SLS3D打印机}
现存的桌面级SLS3D打印机都是在FDM 3D打印机(或者激光切割机)基础上改装而成,XY轴都是使用步进电机+同步带或丝杠的方式拖着激光器进行直线运动,这种机构的最大运动速度只能到达200mm/s左右.
\paragraph{OpenSLS项目}
由美国莱斯大学约旦米勒生理系统和先进材料实验室开发.这个项目的研究的主要方向为粉末烧结材料,是用一台CO2切割机改装而成.
\begin{figure}[ht]
\centering     

\centering

\caption{OpenSLS}
\end{figure}
\newpage

\begin{figure}[ht]
\centering

\caption{步进电机直线模组}
\end{figure}
\subsection{本项目简介}
\paragraph{选题动机}
步进电机直线模组的最大运动速度只能到达200mm/s左右,换言之,激光光斑的移动速度最大只有200mm/s,而激光打标机的振镜电机进行扫描速度能达到1000mms-5000mm/s,是步进电机直线模组的几十倍,为什么不把激光打标机的执行器(两个振镜组成的振镜组)用在SLS3D打印机上面???激光打标机使用的是二维矢量图不能适用于于3D打印,所以开发一个使用Gcode控制的振镜扫描系统是最佳的选择.
\paragraph{目标}
开发一个运行在Arduino Due单片机上的控制程序及配套硬件,可以用数控设备通用的G代码控制振镜,使得振镜兼容常规切片软件,可以用于SLS3D打印,并在此基础上研制使用振镜电机作为XY轴的桌面级SLS3D打印机.
\paragraph{实现方法}
在PC上使用切片软件将3D模型转换成GCode,每行GCode包含了运动轨迹的信息,将GCode通过串口发送到Arduino控制器上,Arduino控制器对GCode进行解释,判断是否需要进行烧结和移动粉缸和改变预热温度的操作及操作数值,对其进行进一步规划后执行,后对PC进行应答而获取下一行GCode,不断执行直至打印完成.
\newpage
%控制理论
\section{控制理论及实现}
本章介绍本项目中振镜电机的控制及补偿算法和步进电机加速度算法.
\subsection{振镜扫描控制}
\subsubsection{单轴振镜电机直线扫描控制}
\paragraph{条件}
设一垂直于振镜旋转轴的直线及原点,反射镜面与直线夹角$\frac{\pi}{4}$,运动目标点坐标x,振镜中心与原点距离d且在原点正上方,反射镜偏角$\alpha$
\begin{figure}[ht]
\centering     

\caption{单轴振镜电机示意图}
\end{figure}
\subparagraph{正运动学:}
\begin{equation}
x=d\tan2\alpha 
\end{equation}
\subparagraph{逆运动学:}
\begin{equation}
\alpha =\frac{1}{2}\arctan\frac{x}{d}
\end{equation}
\paragraph{控制要求}
\subparagraph{输入:}
运动目标点坐标$x$
\subparagraph{输出:}
反射镜偏角$\theta$
\paragraph{控制函数}即逆运动学
\begin{equation}
f(x)=\theta =\frac{1}{2} \arctan\frac{x}{d}
\end{equation}
\clearpage
\subsubsection{双轴振镜电机组平面扫描控制}

\paragraph{条件}
如果简单地使用单轴振镜电机的控制方法

\begin{figure}[ht]

\caption{双轴振镜电机组示意图}
\end{figure}

\subparagraph{正运动学:}
\begin{equation}
\left\{
\begin{array}{c}
x=d\tan2\theta_x \\
y=d\tan2\theta_y\\ 
\end{array}
\right.
\end{equation}
\subparagraph{逆运动学:}
\begin{equation}
\left\{
\begin{array}{l}
2\theta_x = \arctan\frac{x}{d}  \\
2\theta_y = \arctan\frac{y}{d} \\
\end{array}
\right.
\end{equation}
 \paragraph{控制要求}
\subparagraph{输入:}
运动目标点坐标$(x,y)$
\subparagraph{输出:}
x轴振镜反射镜偏角$\theta_x$ , y轴振镜反射镜偏角$\theta_y$
\paragraph{控制函数}
\begin{equation}
f(x,y)=
\left\{
\begin{array}{l}
\theta_x = \frac{1}{2}\arctan\frac{x}{d}  \\
\theta_y = \frac{1}{2}\arctan\frac{y}{d} \\
\end{array}
\right.
\end{equation}
但是如果使用这种控制方式,y轴将会产生枕型失真.
\begin{figure}[ht]
\centering

\caption{扫描正方形图形的枕型失真}
\end{figure}
\newpage
使用上述控制方式控制双轴的振镜组,没有考虑到两个振镜的距离
\paragraph{条件}
设$x$振镜和$y$振镜反射镜中轴之间的距离为$e$,$y$振镜的轴线到扫描平面坐标原点的距离为d,当$x$,$y$轴的光学偏转角分别为$\theta_x$和$\theta_y$时,扫描平面上相应激光斑坐标为$(x,y)$,当$\theta_x=\theta_y=0$时,
\begin{figure}[ht]

\caption{双轴振镜电机组示意图}
\end{figure}
\subparagraph{正运动学:}
\begin{equation}
\left\{
\begin{array}{l}
x=(e+\sqrt{d^2+y^2})\tan 2\theta_x \\
y=d\tan 2\theta_y \\
\end{array}
\right.
\end{equation}
\subparagraph{逆运动学:}
\begin{equation}
\left\{
\begin{array}{l}
2\theta_x = \arctan \frac{x}{e+\sqrt{d^2+y^2}}  \\
2\theta_y = \arctan \frac{y}{d} \\
\end{array}
\right.
\end{equation}
可见,双轴振镜组的运动学模型是复杂的非线性模型.
\newpage
\subsubsection{双轴振镜电机失真分析}
\paragraph{失真产生}
使用单轴扫描方式控制双轴振镜组扫描垂直于x轴的直线时,$\theta_x$不变,设常数$c=2\tan\theta_x$
由$(7)$可得
\begin{equation}
\frac{(x-ce)^2}{c^2 d^2}-\frac{y^2}{d^2}=1
\end{equation}
显然$(9)$描述的曲线为双曲线\\
定义$\varepsilon$为误差 $x_0$为预期位置$x$为实际位置,可见当$e$和$x_0$越大时,x轴偏移$\varepsilon$将越大
\begin{equation}
\varepsilon=x-x_0=(e+\sqrt{d^2+e^2})\tan2\theta_x
\end{equation}
\paragraph{验证}
使用Matlab软件仿真扫描,当$e=5mm$,$d=200mm$扫描长宽为$50mm$的正方形图案\\
\begin{figure}[h]
\centering

\caption{Matlab仿真结果,橙色为预期图形,蓝色为实际扫描图形}
\end{figure}
\subsubsection{振镜控制实现}
解释从串口接收的G代码 若需要移动XY振镜及开关激光 则根据依据设置的每秒插补次数对运动的路径进行分割，对每个插补的XY轴分别计算角度,后转换成DA数值,储存在两个数组中,最后使用定时器让振镜在某个细分时间点运动到DA值制定的位置,这样便完成了直线的扫描.由于计算量比较大,使用了一种机制:在运动时(定时器空隙)接收并计算下一个指令,使两个指令间隔时间减少.
本项目使用的一款振镜电机接收模拟信号为0-5V对应-20°至20°,Arduino Due通过SPI与DAC8852(双路)以50M的速度进行通信,将DA值(DAC8552为16位0-5V对应0-65536)发送给DAC模块.
\subsection{步进电机控制理论及实现}
对于SLS3D打印机来说,一共需要控制3个轴:A轴(铺份刮刀),B轴(粉末储存缸),C轴(打印缸)来完成铺粉过程\\
通过脉冲控制步进电机,脉冲间隔决定电机旋转速度,需要考虑电机的加减速,否则电机将很容易失步
\begin{figure}[ht]
\centering     

\caption{三个直线运动轴}
\end{figure}
\subsubsection{单轴步进电机加减速控制}
\paragraph{条件}
$S$为加速距离(单位:$step$),
$a$为加速度(单位:$step/s^2$),
$v_0$为初始速度(单位:$step/s$),
$v$为目标速度(单位:$step/s$),	
$t$为加速度时间(单位:$s$)
\subparagraph{运动学}{
}
\begin{equation}
s=\frac{v^2-v_0^2}{2a}
\end{equation}
\begin{equation}
v=\sqrt{v_0^2+2aS}
\end{equation}
设$i$为第几步
\begin{equation}
v_i=\sqrt{v_{i-1}^2+2a}
\end{equation}
\paragraph{控制}
使用定时器控制脉冲发送间隔 设:
$P_i$为第i步的间隔时间(单位:$ticks$)
$F$为定时器唤醒周期(单位$ticks/s$)
\begin{equation}
P_i=F/v_i 
\end{equation}
由$(13)$和$(14)$得:
\begin{equation}
P_i=\frac{F}{\sqrt{\frac{F}{P_{i-1}}^2+2a}}
\end{equation}
即
\begin{equation}
P_i=\frac{P_{i-1}}{\sqrt{1+\frac{P_{i-1}^2 2 a}{F^2}}}
\end{equation}

\subparagraph{化简}泰勒展开在$-1\leq n \leq 1$时
\\$\frac{1}{\sqrt{1+n}}\approx1-\frac{n}{2}$
 所以
\begin{equation}
 P_i=P_{i-1}(1-\frac{P_{i-1}^2a}{F^2})
\end{equation}
而$a$ $F^2$为常数
\subsubsection{步进电机控制实现}
在$(17)$中,而$a$ $F^2$在加速度不变时为常量,在程序编译或者控制板开启时可以预先计算在后面的运算中作为常量乘子参与运算\\设$R=\frac{a}{F^2}$则有\\
初始化:
\begin{equation}
P=\frac{F}{\sqrt{V_0^2+2a}}
\end{equation}
加速时:
\begin{equation}
P=P(1-RP^2)
\end{equation}
到达目标速度时:
\begin{equation}
P=P
\end{equation}
减速时:
\begin{equation}
P=P(1+RP^2)
\end{equation}
除了初始化,其他计算只有乘法和加法,因此效率很高.\\
在控制板开启时初始化,计算出第一次的脉冲时间间隔,设定定时器,每次被定时器唤醒就发送一个脉冲并计算下一个脉冲间隔时间,并根据计算出来的脉冲设定定时器的唤醒间隔.
\newpage
\section{机械设计}
本章介绍SLS3D打印机的机械结构都使用Solidworks建模装配\\
一共开发了三代原型机,一个实验平台,将着重介绍第三代.细节详见公开的solidworks源文件
\begin{figure}[ht]
\centering     

\caption{第三代打印机渲染图}
\end{figure}
\subsection{前代打印机}
\paragraph{第一代}
40WCO2激光管 激光振镜 亚克力及铝型材搭建的Z轴
此版本的因为设计时没有考虑到CO2激光功率过大，需要水冷，亚克力不耐热等问题无法使用.\\
\begin{figure}[ht]
\centering     

\caption{第一代打印机实物图}
\end{figure}
\newpage
\paragraph{第二代}
使用半导体激光 激光振镜 铝板 铝型材搭建的第二代原型机
\begin{figure}[ht]
\centering     

\centering     

\caption{第二代打印机渲染图及实物图}
\end{figure}
\subsection{二维烧结实验平台}
二维烧结实验平台用于单层烧结实验,使用5W半导体激光(450nm)及激光振镜,并在底部加装加热板对粉末预热
\begin{figure}[ht]
\centering     

\centering     

\caption{二维烧结实验平台模型图及实物图}
\end{figure}
\newpage
\subsection{第三代SLS打印机}
打印机由三部分构成:\\
激光机构(XY轴)\\
粉末机构(ABC轴)\\
加热机构
\paragraph{激光机构}
激光机构由两个振镜电机依照上章所述的方式安装,使用了一个5W450nm半导体激光器.
\begin{figure}[ht]
\centering

\caption{激光机构}
\end{figure}
\paragraph{粉末机构}
粉末机构的作用是覆盖一层粉末到已烧结完成的打印件上面,从而完成整个三维堆积的过程\\
具体的过程如下:\\初始状态时,粉末储存缸(B轴)的推杆降到最低,而打印缸推杆(C轴)上升到距离缸口极小的距离,将两个缸都装满粉,刮刀往返运动一次,这时打印缸内便有了一层薄而又均匀的粉末,进行平面烧结后,打印缸下降一段距离,粉末储存缸上升一段距离,这时便有部分粉末从粉末储存缸的缸口溢出,刮刀往返一次,将粉末储存缸的粉末带到打印缸,并铺匀,这时,第一次平面烧结得到的打印件上面便覆盖了一层粉末,继续扫描,扑粉,不断重复这个过程.
\begin{figure}[ht]
\centering

\caption{ 粉末机构}
\end{figure}
\newpage
\paragraph{加热机构}
使用两个红外加热管对粉末进行预热
\begin{figure}[ht]
\centering

\caption{加热机构}
\end{figure}
\paragraph{整机}整机模型图
\begin{figure}[ht]
\centering

\caption{整机}
\end{figure}

%结构
\newpage
\section{结果}
\paragraph{单层烧结}
\subparagraph{扫描性能}
在不考虑激光功率的情况下,振镜电机在GCode的控制下速度可以达到1000mm/s至5000mm/s,速度越快,精度越低.
\subparagraph{烧结结果}
使用XY测试平台使用黑色碳粉末和白色PLA粉末混合,增加激光被吸收的热量,进行单层烧结实验,可以得到精密结合的薄塑料片.
\begin{figure}[ht]
\centering


\caption{单层烧结}
\end{figure}

\paragraph{多层烧结(即3D打印)}
使用第三代打印机对粉末进行进行多层烧结,层与层之间粘黏良好,可以打印出许多结构及其复杂(其他打印机难以打印出来)的模型.
\begin{figure}[ht]


\caption{多层烧结(3D打印)}
\end{figure}
\newpage
%结论
\section{结论}
本项目成功开发一个运行在Arduino Due单片机上的控制系统,可以用数控设备通用的G代码控制振镜,使得振镜电机组兼容常规3D切片软件,可以用于SLS3D打印,并在此基础上开发使用振镜电机作为XY轴的桌面级SLS3D打印机,并使用腌制出来的SLS3D打印机成功打印出塑料打印件\\
作为一个系统,在根据不同材料要求更换激光器的功率波长后,理论上可以兼容其他材料,如金属,铸造蜡,光敏树脂等.
%致谢
\section{致谢}
在项目的研究过程中,潮州市金山中学、潮州市科学技术协会、指导老师黄胜刚给了我很大的帮助.
%参考文献
\section{参考文献}
赵毅, 卢秉恒. 振镜扫描系统的枕形畸变校正算法[J]. 中国激光, 2003, 30(3): 216-218.\\
Eiderman A. Real Time Stepper Motor Linear Ramping Just by Addition and Multiplication[J].\\
\end{document}

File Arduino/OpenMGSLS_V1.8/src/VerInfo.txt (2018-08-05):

Version Information
版本信息

G代码N行数及*checksum校检 
DAVal数组由动态改为静态 解决了打印途中死机现象

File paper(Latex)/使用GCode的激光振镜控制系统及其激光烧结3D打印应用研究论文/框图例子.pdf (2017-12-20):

使⽤⾮线性最⼩ ⼆乘法得到 X0; step = 0; step < count?; 得到新状态 PN = P + scale × rand, 计算⽬标; 函数差 ∆f; FAccept < rand?; 记录新状态 X = XN , f = f(XN ); T = T × a, scale =; scale × b; step + +

1

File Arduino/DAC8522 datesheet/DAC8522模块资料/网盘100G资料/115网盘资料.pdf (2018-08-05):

梦想电子工作室

联系方式：http://mcu-dream.taobao.com

# 115 网盘资料

礼包提取：
http://115.com/lb/5lbapw5st1cb#梦想电子工作室，大小：103.06GB
115 网盘礼包码：5lbapw5st1cb

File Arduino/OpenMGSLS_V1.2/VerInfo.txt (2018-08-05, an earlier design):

Version Information
版本信息

Reconstruct the program 
重构程序框架

Optimize serial port reception
优化串口接收

Accurate control of the galvanometer speed is performed using the duetimer.h
使用duetimer库进行对振镜速度精确控制

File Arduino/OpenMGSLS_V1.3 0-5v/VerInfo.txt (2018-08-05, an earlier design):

Version Information
版本信息

优化串口
 
优化算法

使用面向对象的编程思想导致程序运行较慢，在下一版本将解决这一问题

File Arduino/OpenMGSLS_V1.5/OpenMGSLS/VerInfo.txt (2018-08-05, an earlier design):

Version Information
版本信息

调整串口速率（650000不够稳定 ）

在定时器中断间隔接受并计算下一条指令

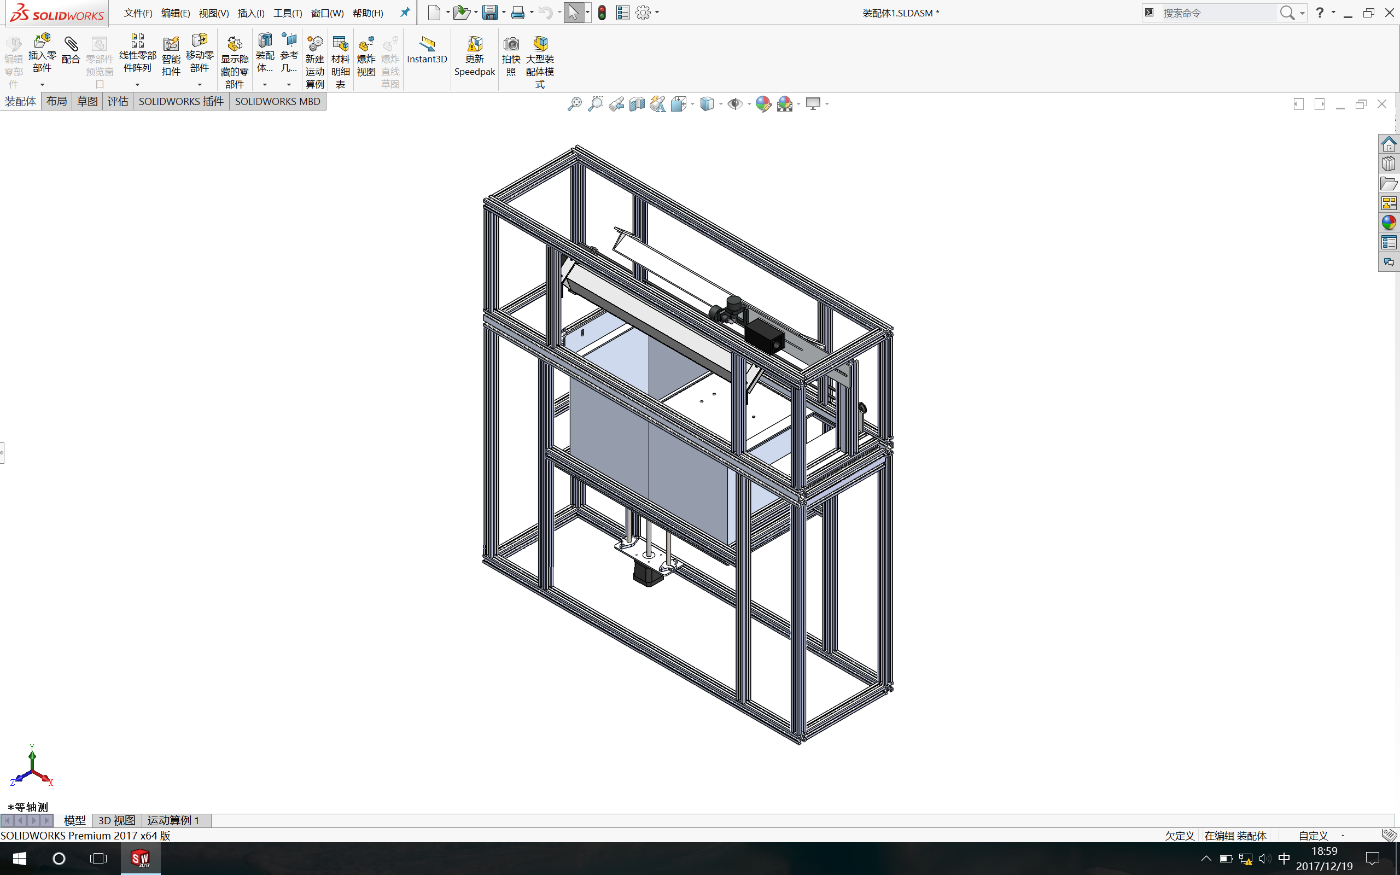
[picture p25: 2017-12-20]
paper(Latex)/图片备份/MGSLS3-5.png

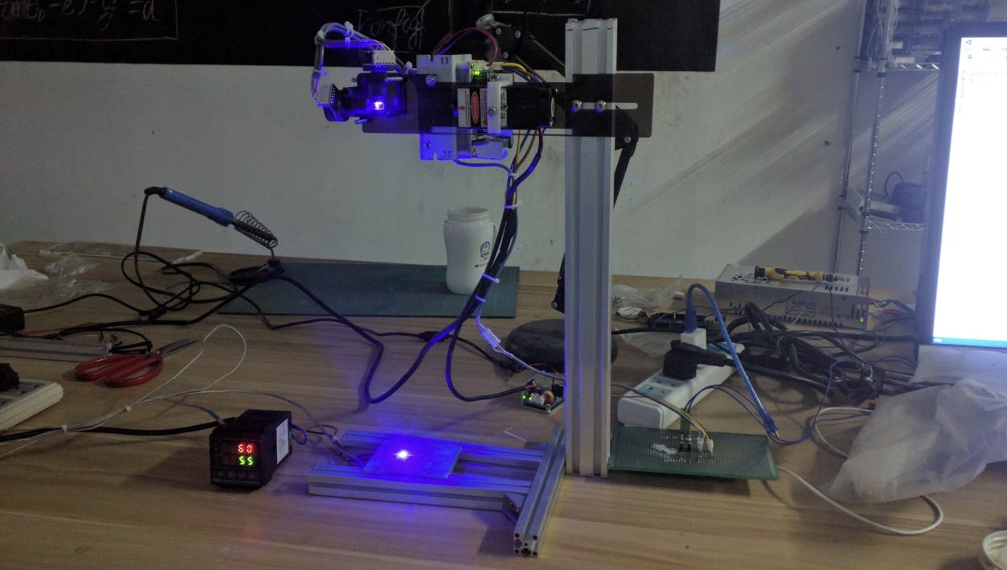
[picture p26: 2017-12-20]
paper(Latex)/图片备份/SW1.jpg

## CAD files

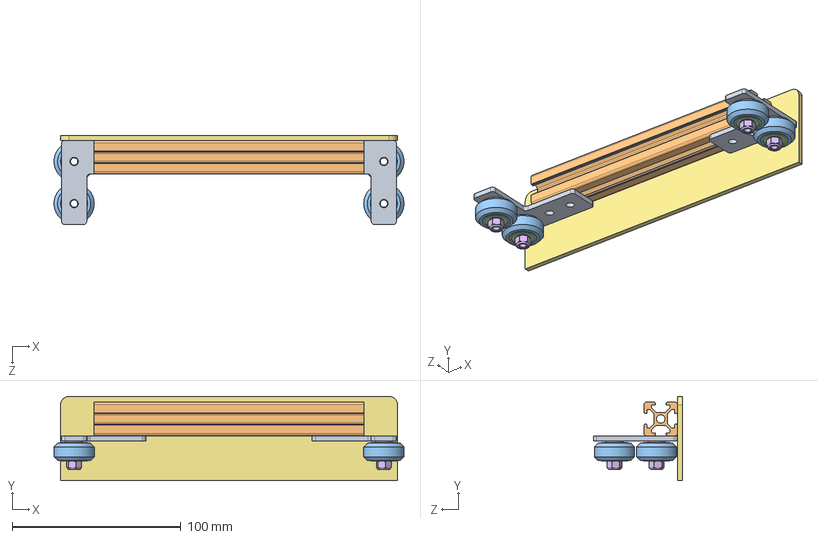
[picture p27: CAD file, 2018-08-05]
Cad_Drawing/OpenMGSLS V1.3/装配体/2级装配体/A轴1.SLDASM
207.7 x 50.0 x 53.0 mm
A轴-滑车架 x 2
A轴-2020X160
A轴-Solid V Wheel x 4
A轴-Ball Bearing 5 x 16 x 5 x 8
A轴-Precision Shim 10 x 5 x 1 x 8
A轴-Nylon Insert Lock Nut M5 x 4
A轴-刮刀

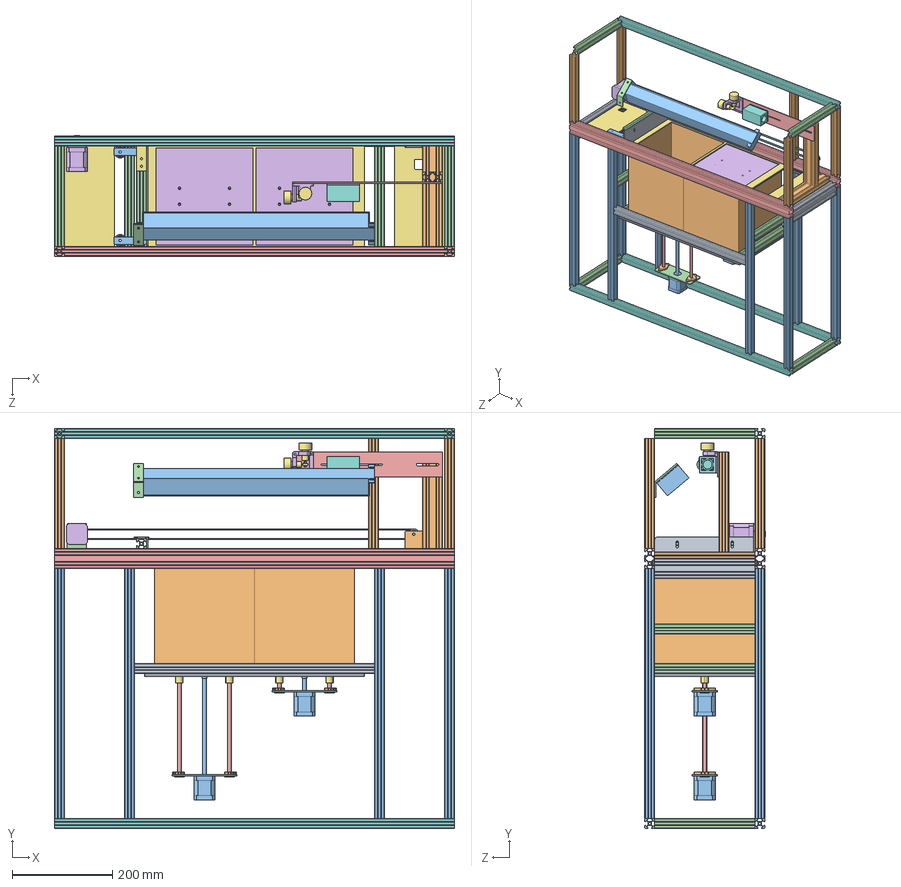
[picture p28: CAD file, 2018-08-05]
Cad_Drawing/OpenMGSLS V1.3/装配体/3级装配体/装配体1.SLDASM
800.0 x 800.0 x 241.0 mm
BC轴-托板 x 2
BC轴-光轴架8mm x 8
BC轴-42步进电机丝杠250mm x 2
BC轴-电机架 x 2
BC轴-光轴8X250mm x 4
BC轴-粉缸面 x 2
BC轴-光轴架 x 4
BC轴-丝杠螺母 x 2
BC轴-2020X480 x 2
BC轴-200X200X2X220 x 2
BC轴-2020X500 x 8
BC轴-2020X200 x 8
BC轴-2040X800 x 2
BC轴-上盖板1
BC轴-上盖板2
BC轴-2020X800 x 3
BC轴-2040X200 x 2
BC轴-2020X220 x 5
XY轴-连接板
XY轴-振镜支架
XY轴-振镜 x 2
XY轴-半导体激光
XY轴-激光垫片
XY轴-2040X200 x 2
A轴-滑车架 x 2
A轴-2020X160
A轴-Solid V Wheel x 4
A轴-Ball Bearing 5 x 16 x 5 x 10
A轴-Precision Shim 10 x 5 x 1 x 9
A轴-Nylon Insert Lock Nut M5 x 5
A轴-刮刀
A轴-Idler Pulley Plate
A轴-Smooth Idler Pulley Wheel
A轴-Motor Mount Plate Nema 17
A轴-GT2 Timing Pulley 30 Tooth
A轴-Nema 17 Stepper Motor
A轴-同步带连接
GT2 Belt

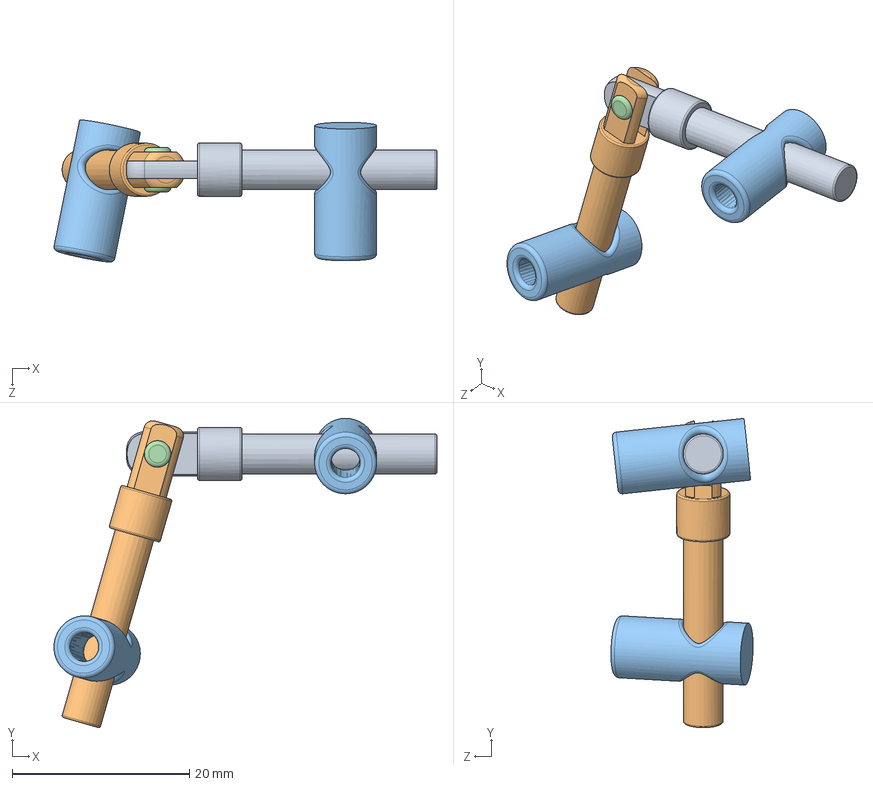
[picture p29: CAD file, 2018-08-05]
Cad_Drawing/铝型材零件图solidworks/任意角度连接件/新建文件夹/2020任意角度连接件.SLDASM
43.2 x 34.9 x 16.0 mm
2020任意角连接件a
2020任意角连接件b
2020任意角连接件c x 2
2020任意角连接件d

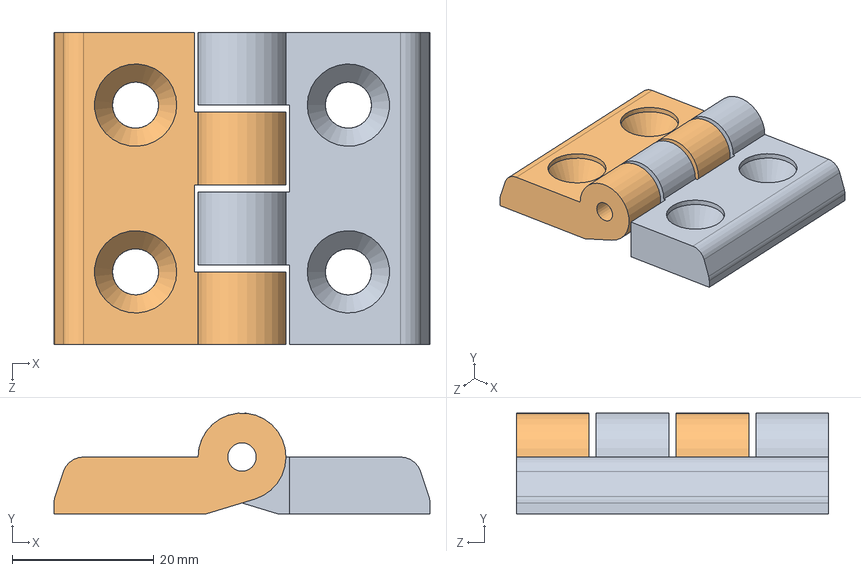
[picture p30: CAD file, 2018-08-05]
Cad_Drawing/铝型材零件图solidworks/合页/3030尼龙合页/3030尼龙合页组1.SLDASM
53.0 x 14.2 x 44.0 mm
3030尼龙合页左1
3030尼龙合页右11

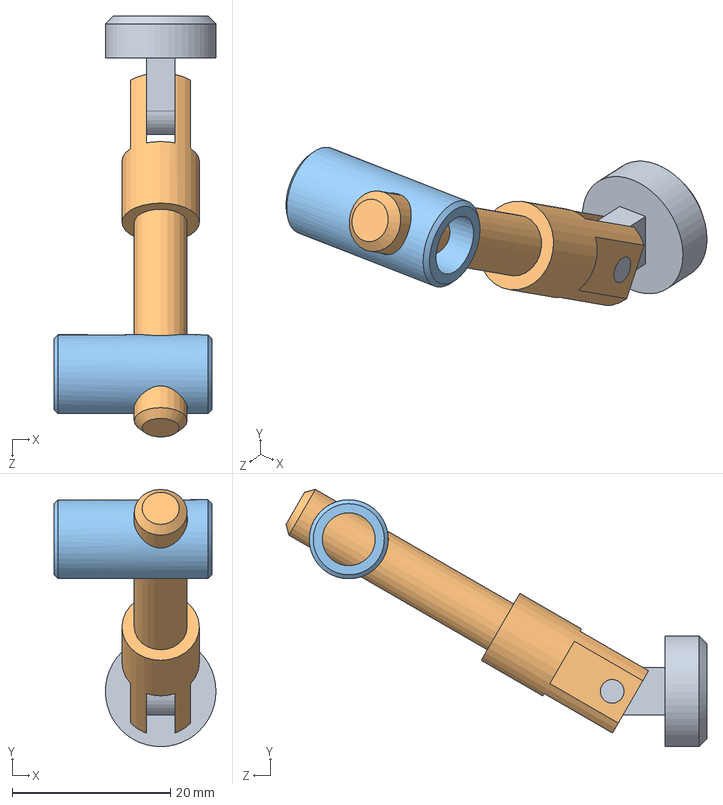
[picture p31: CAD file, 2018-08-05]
Cad_Drawing/铝型材零件图solidworks/斜角、任意角连接销/3030连接销组.SLDASM
20.5 x 32.6 x 53.3 mm
斜角连接销-头3030
斜角连接销杆3030
螺母1

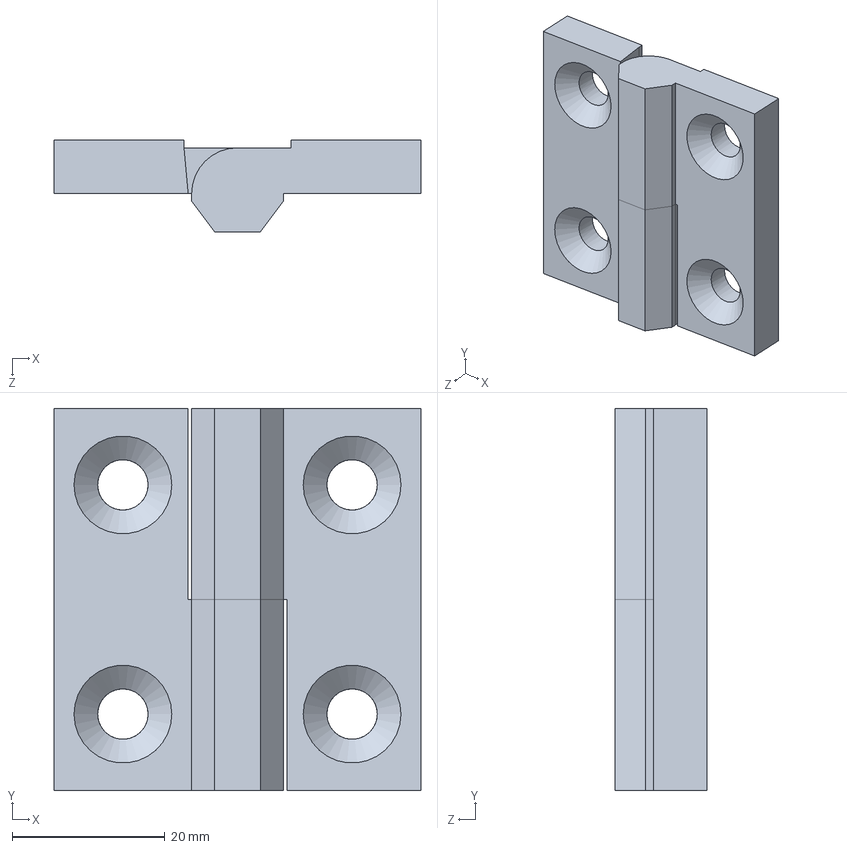
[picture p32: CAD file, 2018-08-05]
Cad_Drawing/铝型材零件图solidworks/蹄脚/3030可拆分合页.SLDASM
48.0 x 50.0 x 12.0 mm
3030可拆分合页 x 2

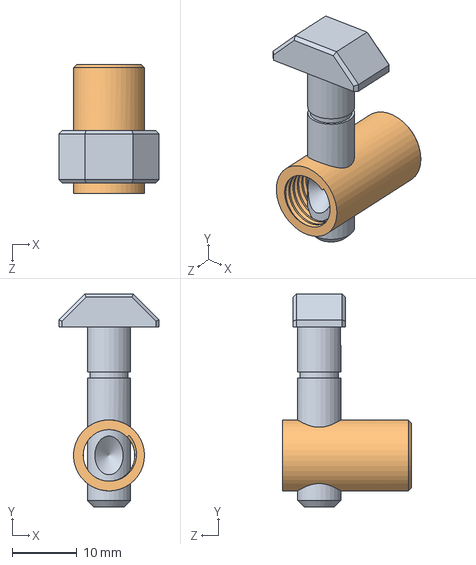
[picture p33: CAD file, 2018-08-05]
Cad_Drawing/铝型材零件图solidworks/连接销/连接销组.SLDASM
15.5 x 33.0 x 20.0 mm
直角连接销-杆
直角连接销

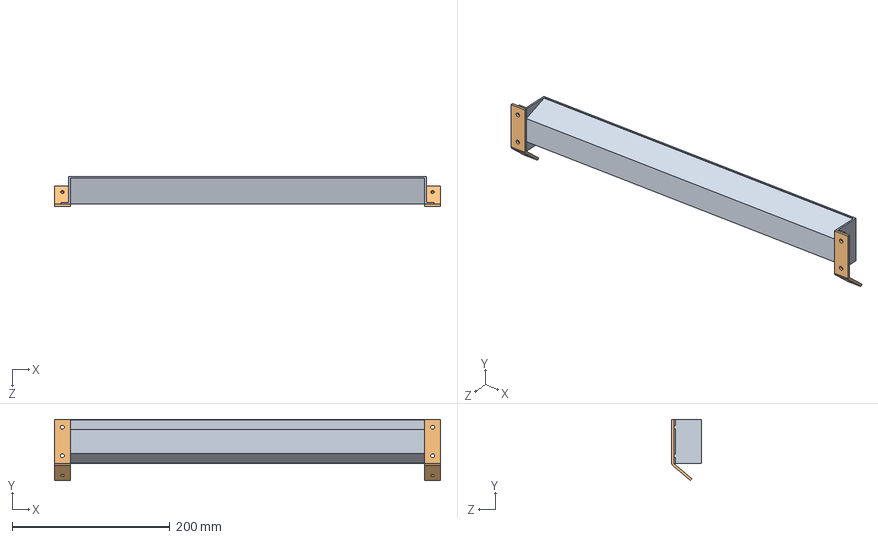
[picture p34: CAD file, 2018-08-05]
Cad_Drawing/OpenMGSLS V1.3/装配体/1级装配体/加热器.SLDASM
490.0 x 77.6 x 38.0 mm
BC轴-加热器
BC轴-加热器架 x 2

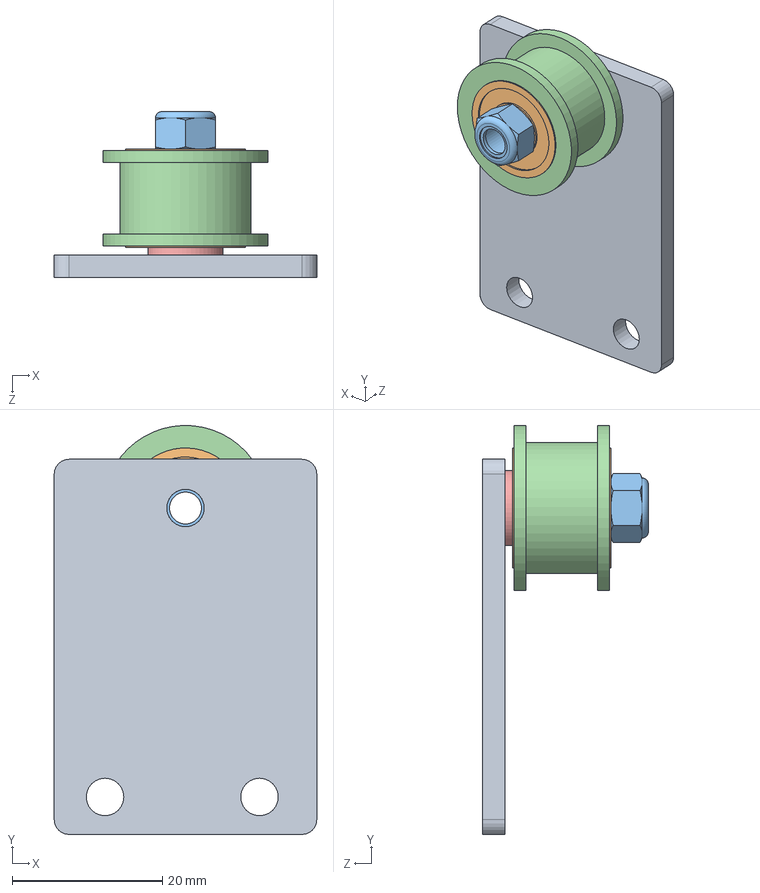
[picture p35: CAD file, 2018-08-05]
Cad_Drawing/OpenMGSLS V1.3/装配体/2级装配体/A轴2.SLDASM
35.0 x 54.5 x 22.1 mm
A轴-Idler Pulley Plate
A轴-Ball Bearing 5 x 16 x 5 x 2
A轴-Nylon Insert Lock Nut M5
A轴-Smooth Idler Pulley Wheel
A轴-Precision Shim 10 x 5 x 1

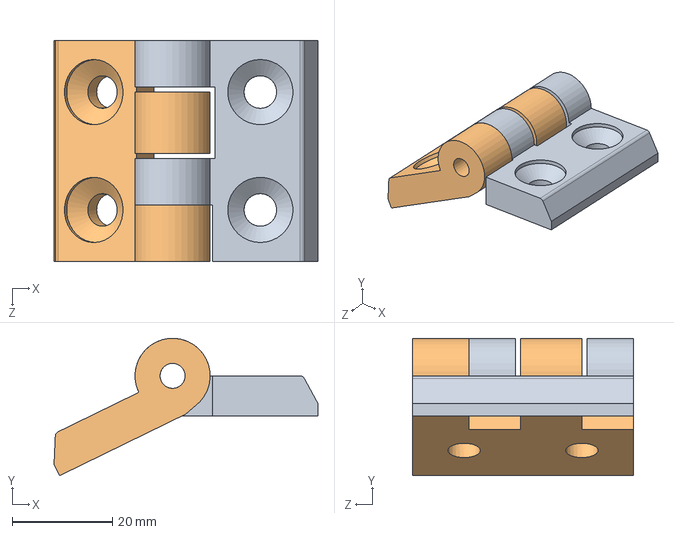
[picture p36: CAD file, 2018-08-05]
Cad_Drawing/铝型材零件图solidworks/合页/3040尼龙合页/3040尼龙合页组.SLDASM
52.6 x 27.4 x 44.0 mm
3040尼龙合页左
3040尼龙合页右

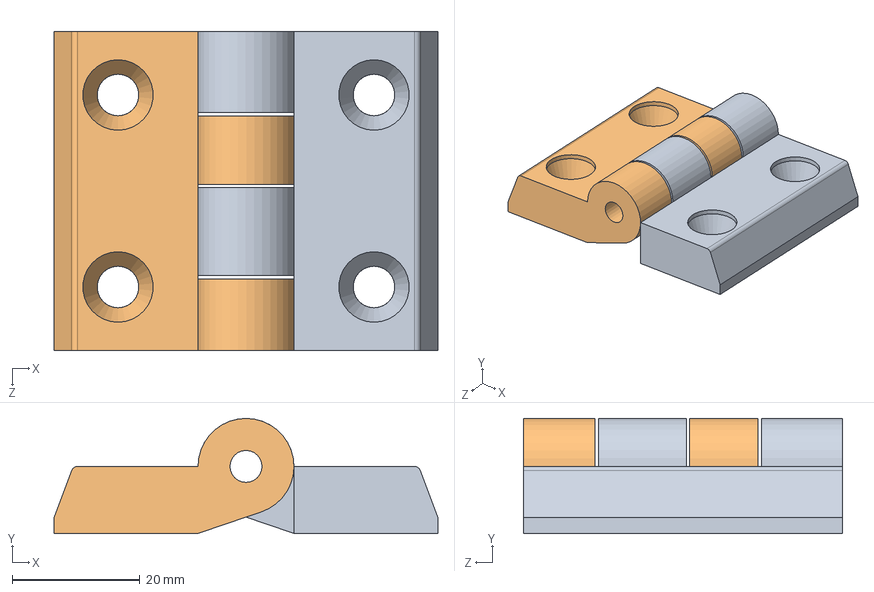
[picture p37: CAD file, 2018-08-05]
Cad_Drawing/铝型材零件图solidworks/合页/4040尼龙合页/4040尼龙合页组.SLDASM
60.0 x 18.0 x 49.9 mm
4040尼龙合页右
4040尼龙合页左

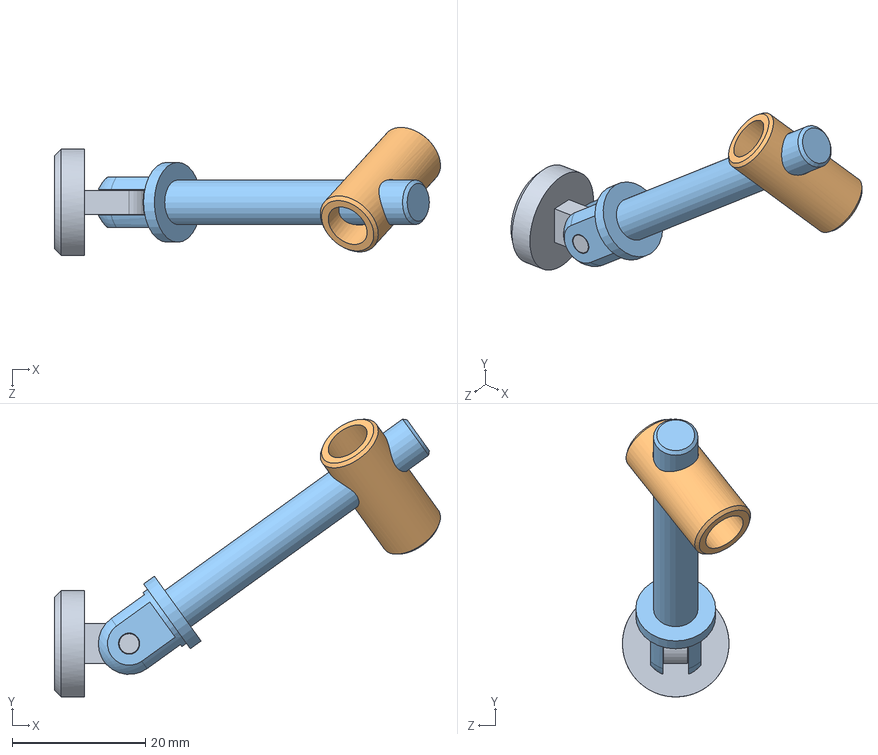
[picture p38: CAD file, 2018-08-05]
Cad_Drawing/铝型材零件图solidworks/斜角、任意角连接销/4040/4040斜角连接销组.SLDASM
57.9 x 41.7 x 19.2 mm
4040连接销－头
螺母1
连接销

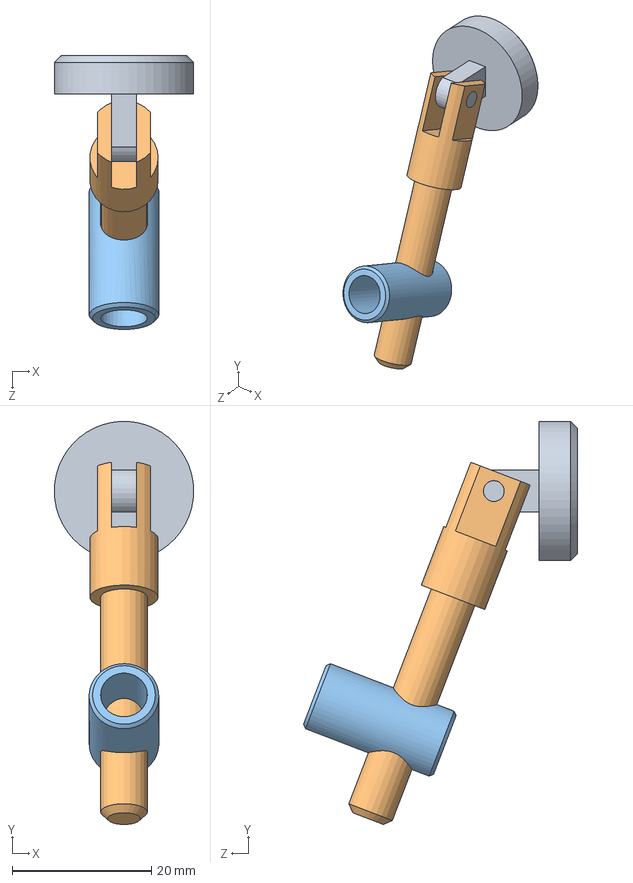
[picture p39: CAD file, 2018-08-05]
Cad_Drawing/铝型材零件图solidworks/斜角、任意角连接销/4545/4545斜角连接销.SLDASM
20.0 x 57.8 x 39.3 mm
斜角连接销-头4545
斜角连接销杆4545
螺母1

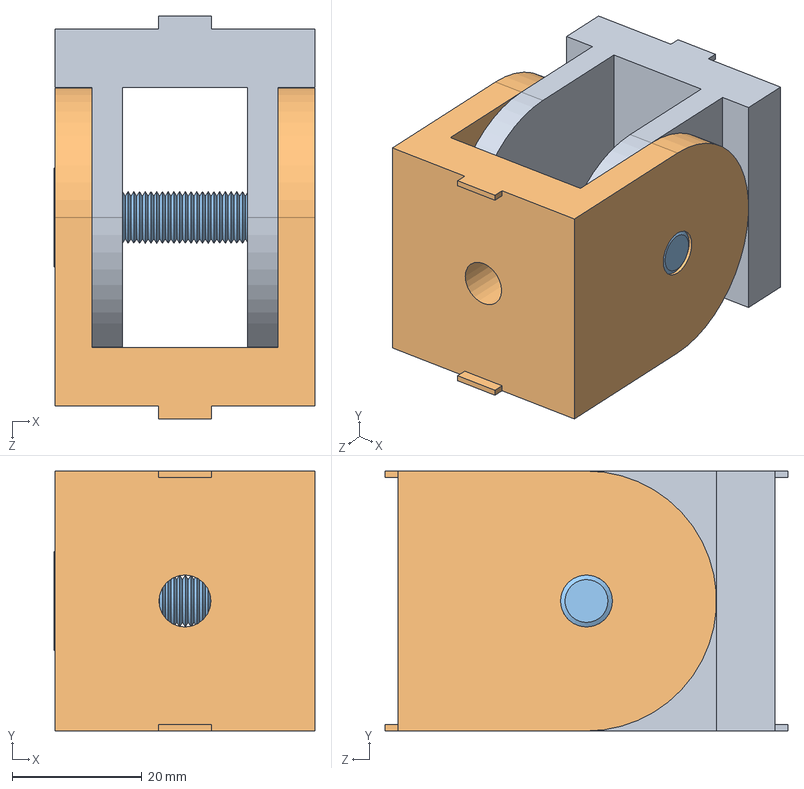
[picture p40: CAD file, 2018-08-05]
Cad_Drawing/铝型材零件图solidworks/螺丝螺母/4040铰链组.SLDASM
40.1 x 40.0 x 62.0 mm
活动铰链-内
活动铰链-外
M8X40平机螺栓

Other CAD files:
Cad_Drawing/OpenMGSLS V1.3/装配体/1级装配体/振镜总装.SLDASM
Cad_Drawing/铝型材零件图solidworks/蹄脚/门插销.SLDASM
Cad_Drawing/铝型材零件图solidworks/连接板/挂钩.SLDASM
Cad_Drawing/铝型材零件图solidworks/连接板/活动铰链/2020/2020活动铰链.SLDASM
Cad_Drawing/OpenMGSLS V1.0/Zaxis/装配体/Box.SLDASM
Cad_Drawing/OpenMGSLS V1.0/Zaxis/装配体/Z轴装配体.SLDASM
Cad_Drawing/OpenMGSLS V1.0/Zaxis/装配体/亚克力装配体.SLDASM
Cad_Drawing/OpenMGSLS V1.0/Zaxis/装配体/外框架装配体.SLDASM
Cad_Drawing/OpenMGSLS V1.0/Zaxis/装配体/装配体.SLDASM
Cad_Drawing/OpenMGSLS V1.0/Zaxis/装配体/装配体1.SLDASM
Cad_Drawing/OpenMGSLS V1.0/Zaxis/装配体/装配体2.SLDASM
Cad_Drawing/OpenMGSLS V1.0/Zaxis/装配体/装配体3.SLDASM
Cad_Drawing/OpenMGSLS V1.0/Zaxis/零件/2020.SLDPRT
Cad_Drawing/OpenMGSLS V1.0/Zaxis/零件/2020R.SLDPRT
Cad_Drawing/OpenMGSLS V1.0/Zaxis/零件/2020RX300.SLDPRT
Cad_Drawing/OpenMGSLS V1.0/Zaxis/零件/2020RX500.SLDPRT
Cad_Drawing/OpenMGSLS V1.0/Zaxis/零件/2020RX600.SLDPRT
Cad_Drawing/OpenMGSLS V1.0/Zaxis/零件/2020R盖.SLDPRT
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

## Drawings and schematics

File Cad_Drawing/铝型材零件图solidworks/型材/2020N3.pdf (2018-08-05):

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

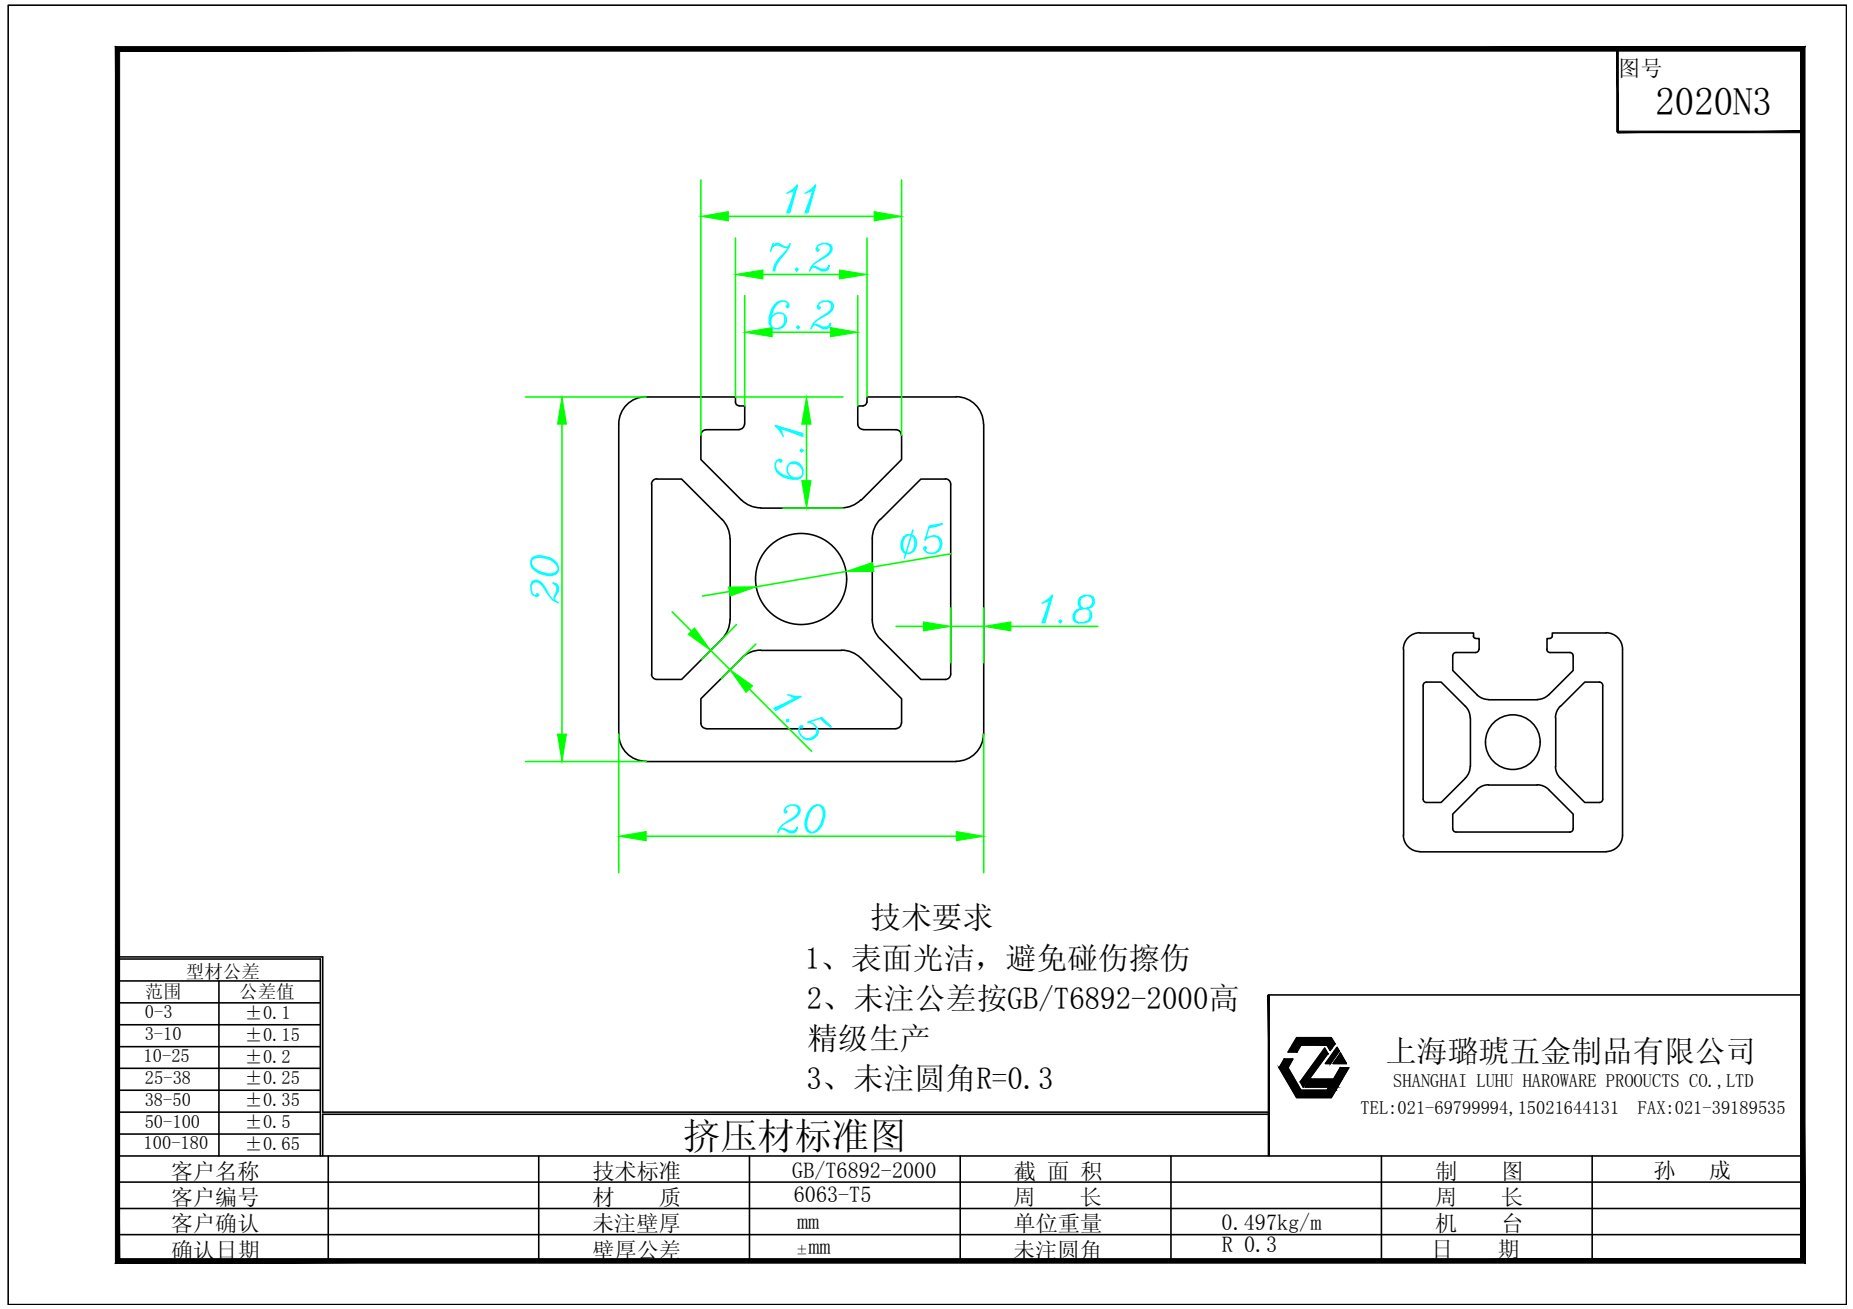
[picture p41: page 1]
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

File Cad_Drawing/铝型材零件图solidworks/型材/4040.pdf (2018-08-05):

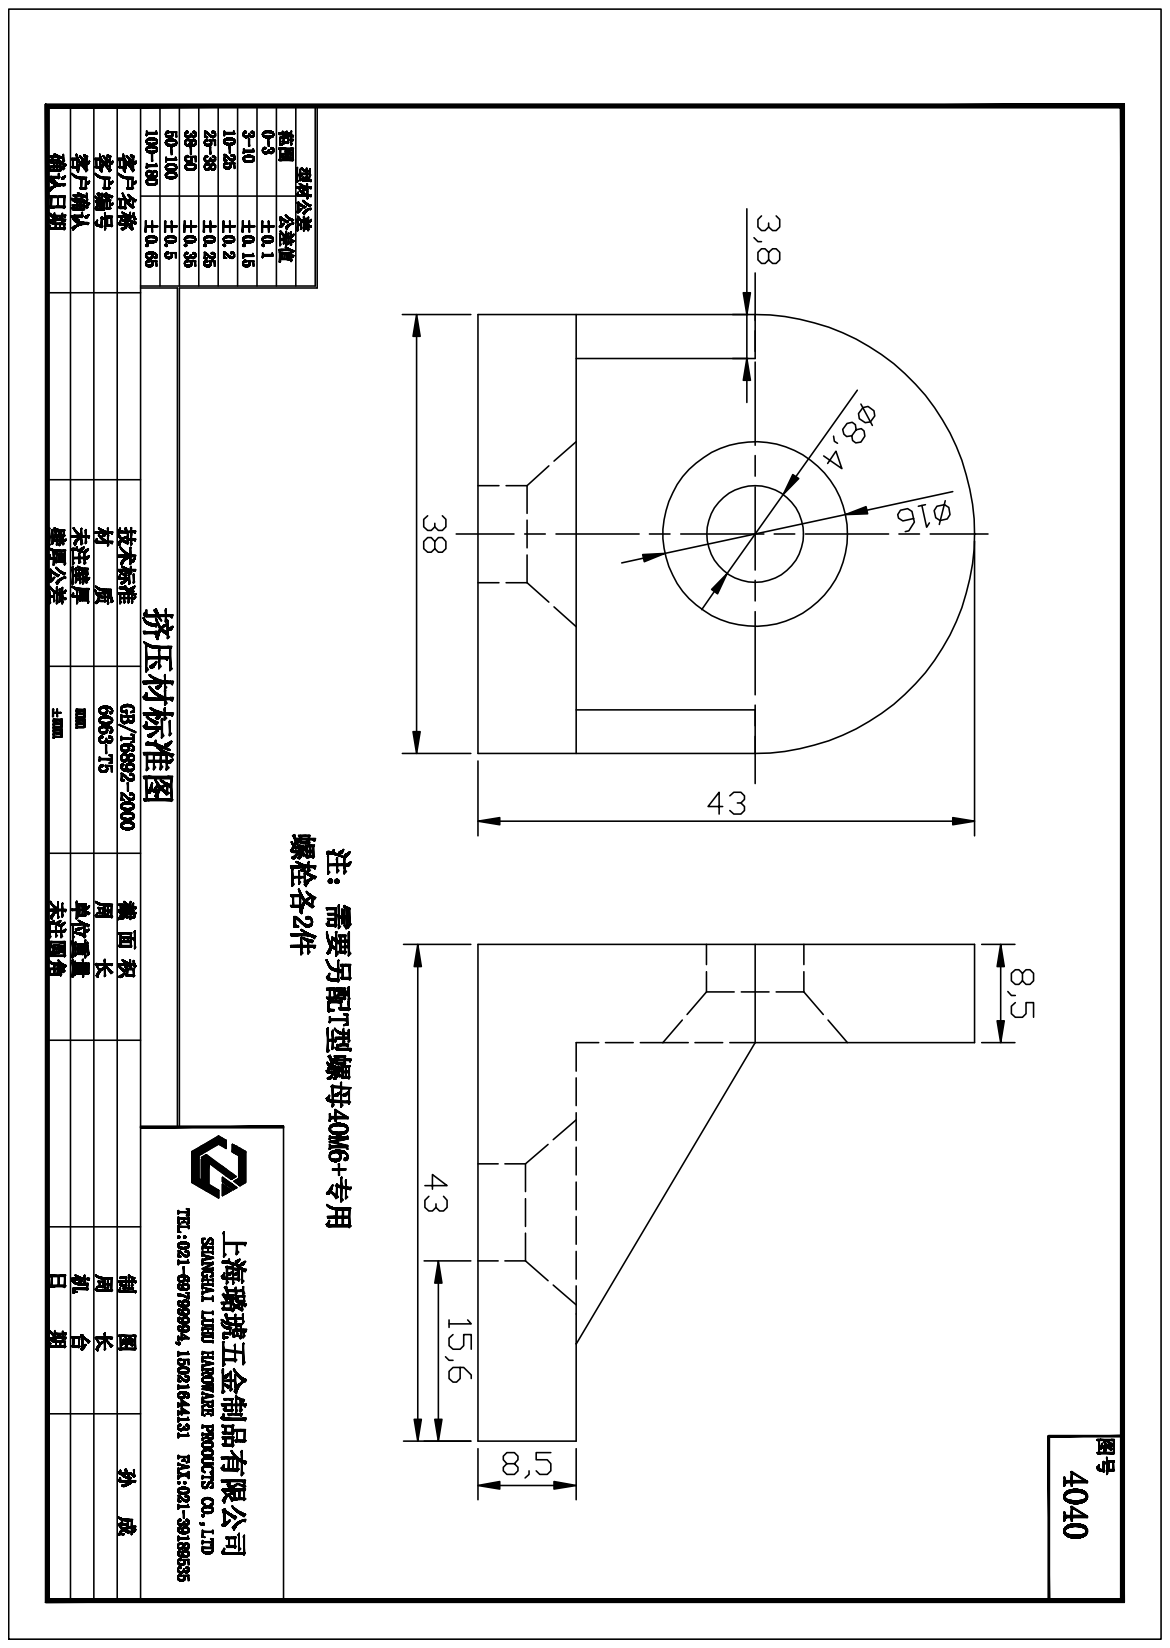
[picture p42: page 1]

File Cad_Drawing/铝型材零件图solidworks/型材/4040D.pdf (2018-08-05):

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

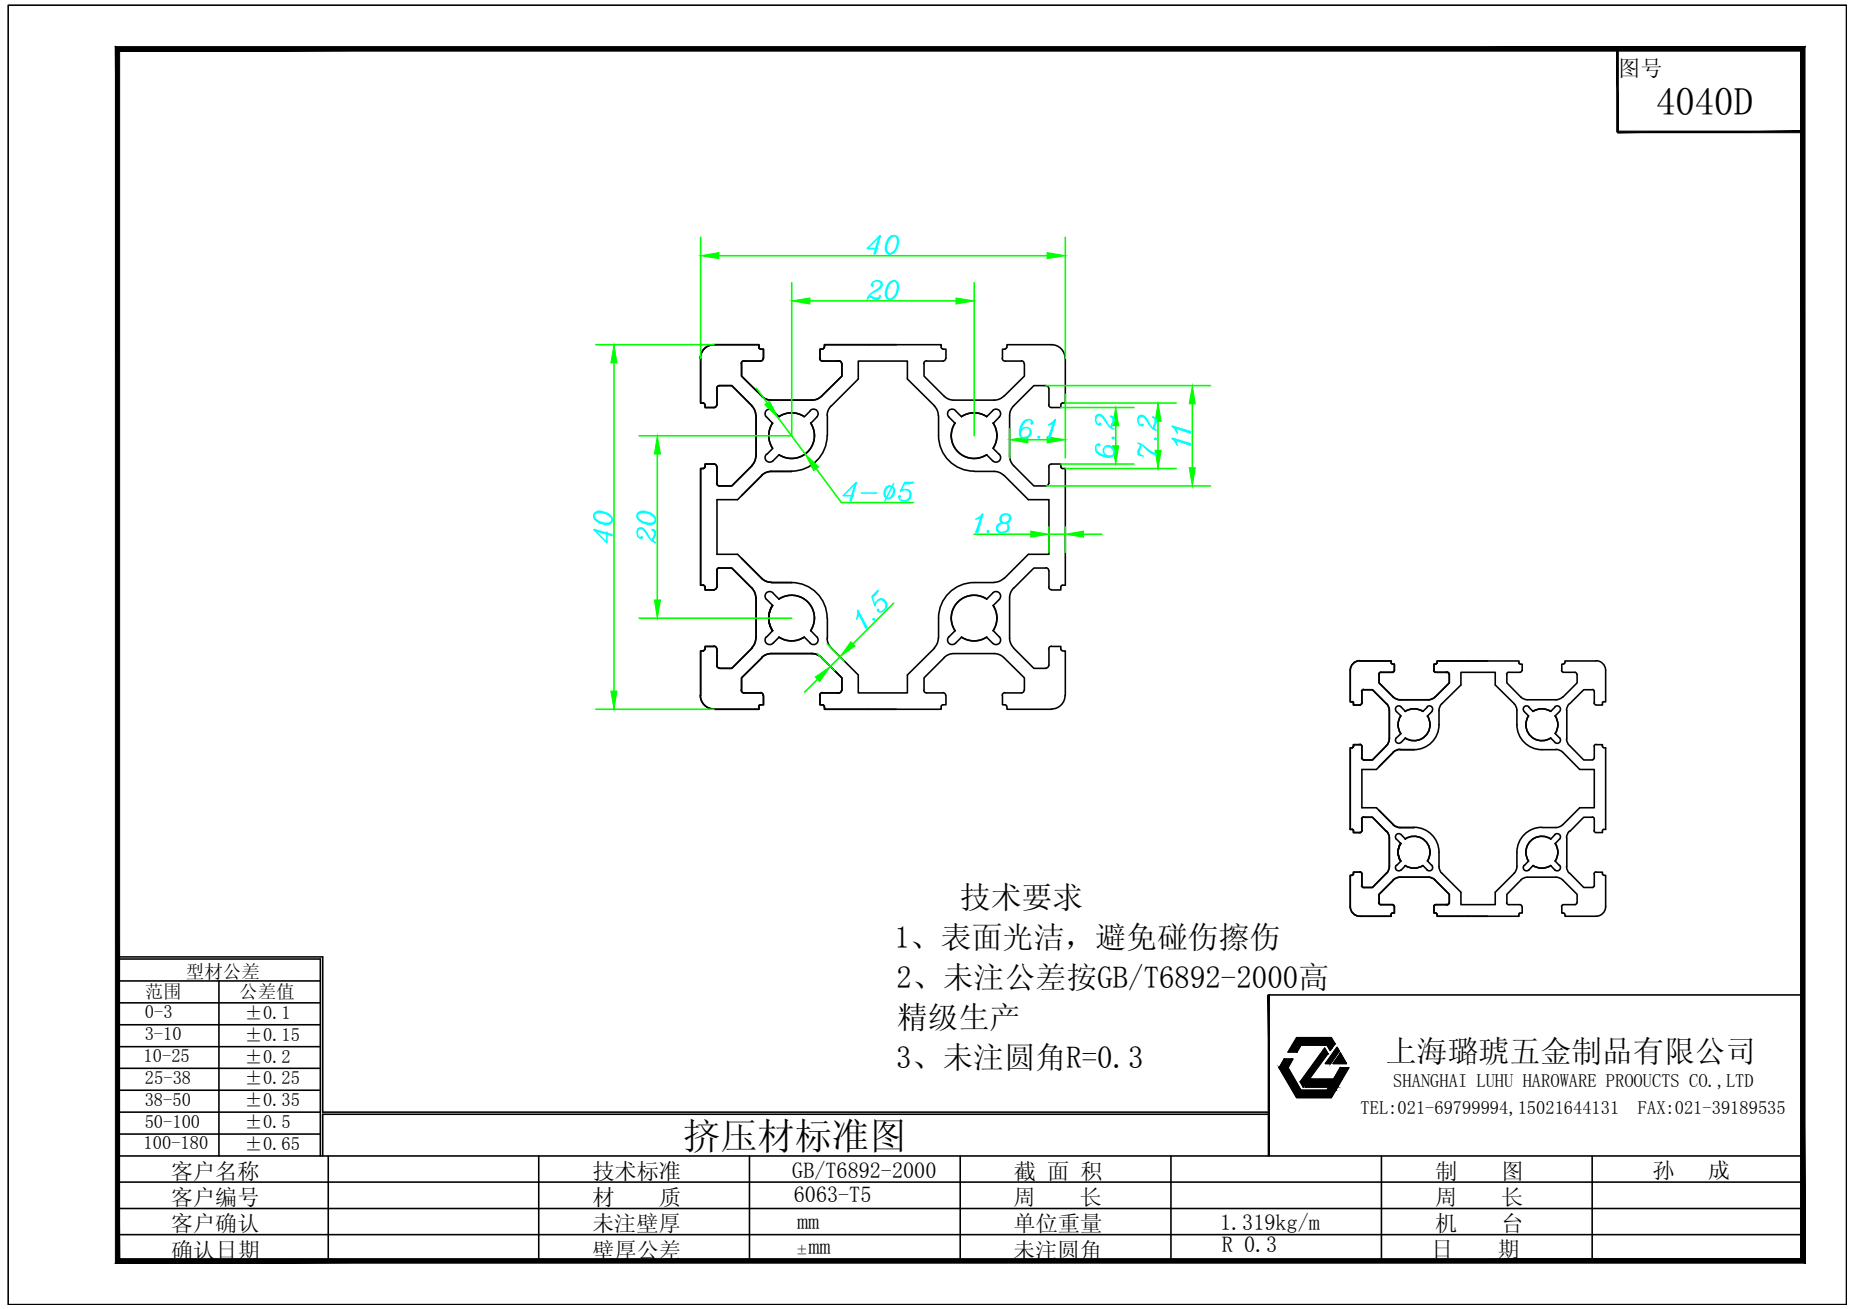
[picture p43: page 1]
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

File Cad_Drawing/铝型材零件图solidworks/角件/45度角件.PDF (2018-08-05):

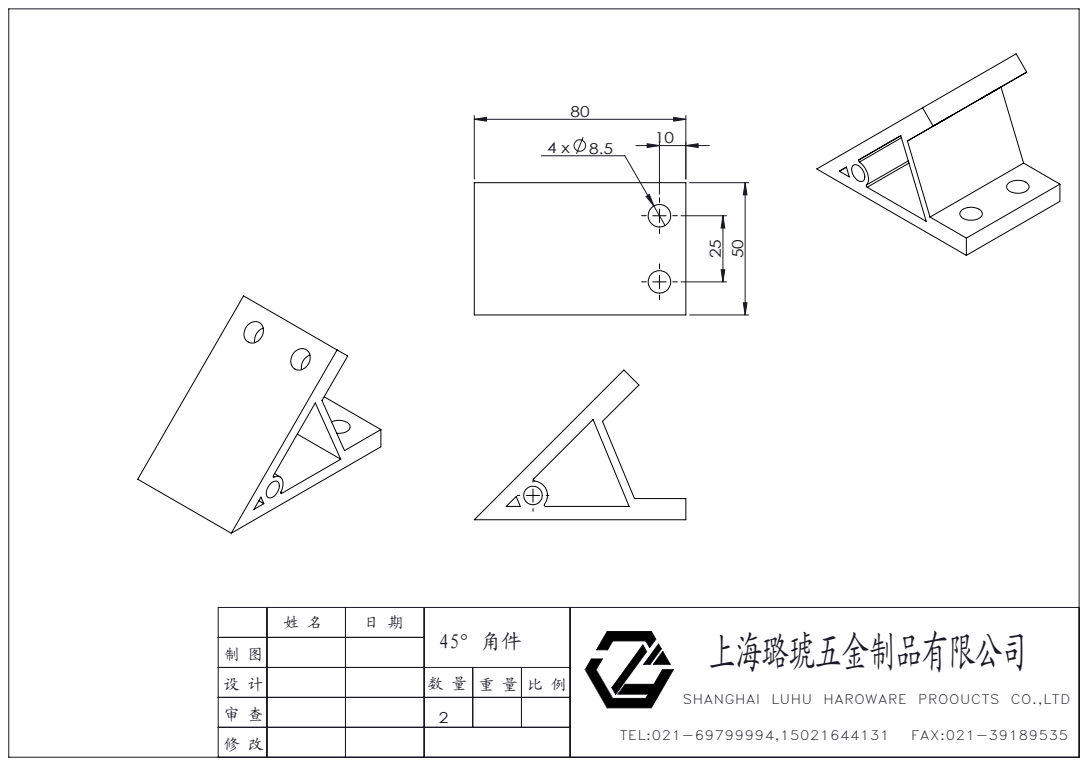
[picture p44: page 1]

SHANGHAI LUHU HAROWARE PROOUCTS CO.,LTD

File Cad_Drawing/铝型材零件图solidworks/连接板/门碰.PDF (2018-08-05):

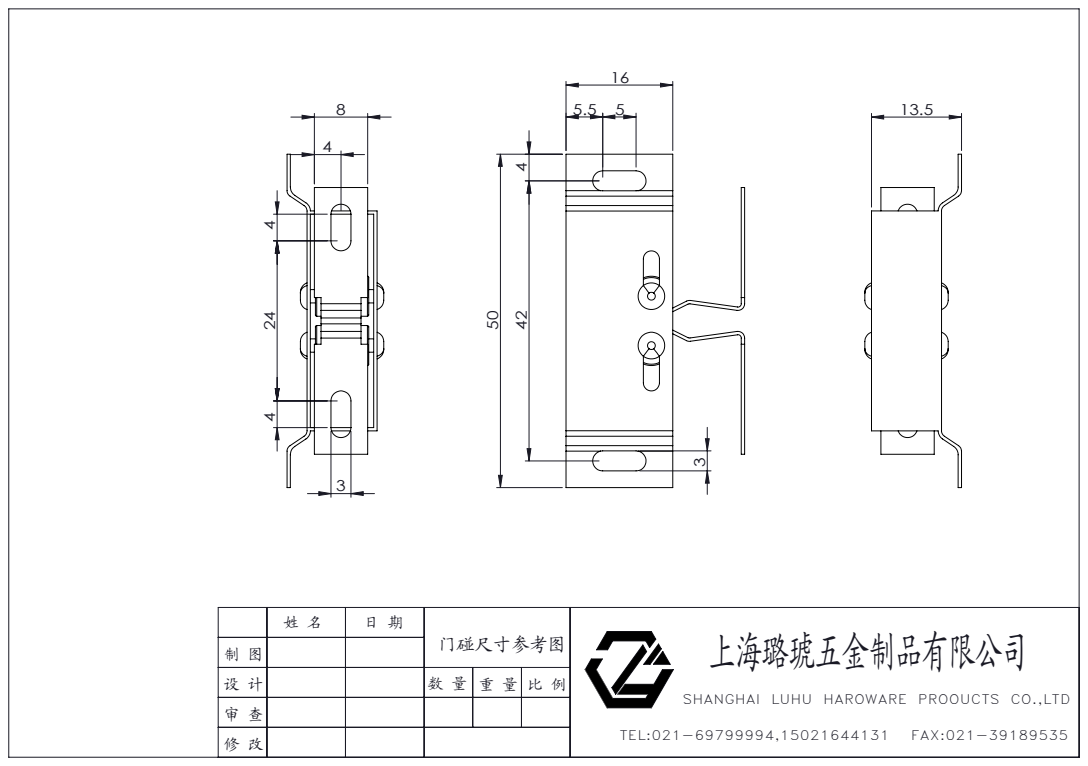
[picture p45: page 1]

SHANGHAI LUHU HAROWARE PROOUCTS CO.,LTD

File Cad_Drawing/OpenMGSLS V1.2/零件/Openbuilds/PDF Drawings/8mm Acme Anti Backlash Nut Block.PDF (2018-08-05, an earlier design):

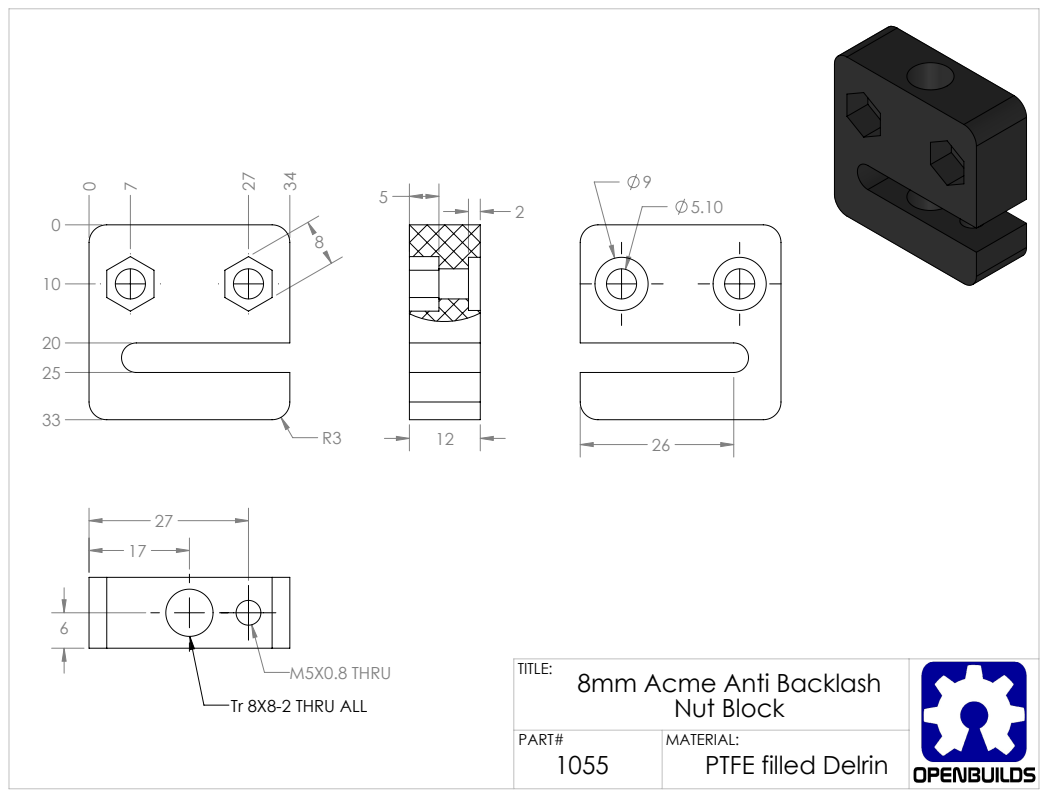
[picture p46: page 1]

M5X0.8 THRU
Tr 8X8-2 THRU ALL

TITLE: 8mm Acme Anti Backlash Nut Block

PART# 1055 | MATERIAL: PTFE filled Delrin

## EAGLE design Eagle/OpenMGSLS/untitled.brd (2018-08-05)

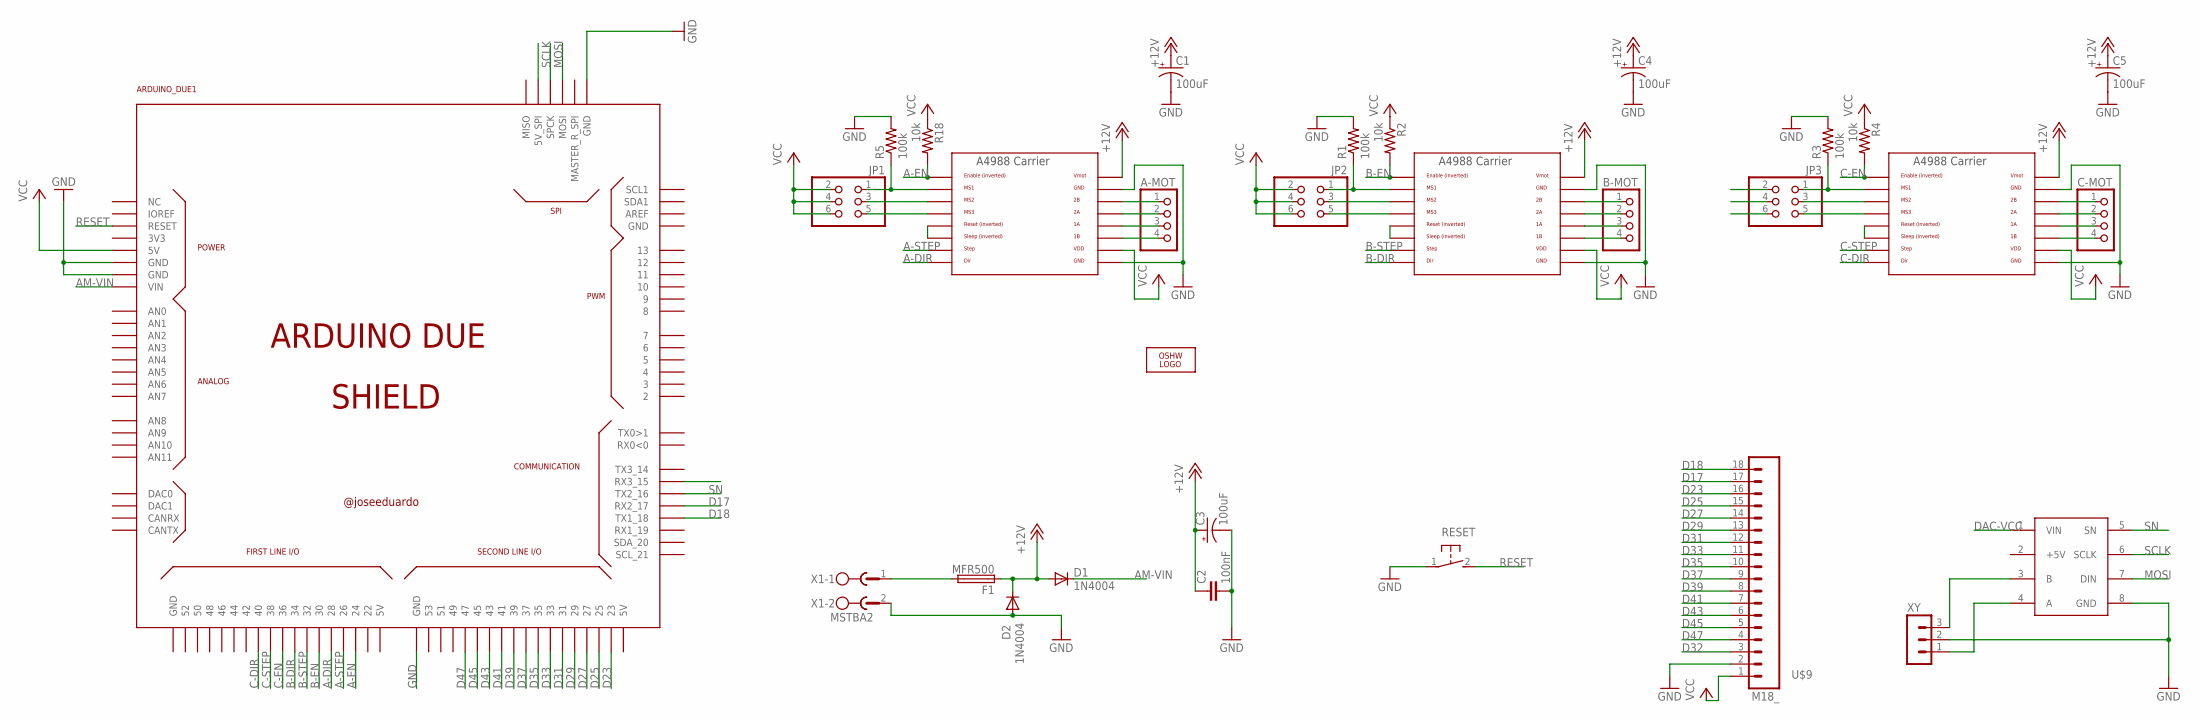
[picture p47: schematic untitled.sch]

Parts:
A-MOT: PINHD-1X4; 1X04
ARDUINO_DUE1: ARDUINO_DUE_SHIELD
B-MOT: PINHD-1X4; 1X04
C1, C3, C4, C5: 100uF; 153CLV-0605
C2: 100nF; C0805
C-MOT: PINHD-1X4; 1X04
D1, D2: 1N4004; DO41-10
F1: MFR500
JP1, JP2, JP3: PINHD-2X3; 2X03
LOGO1: OSHW_LOGO_6MILX0200-NT; OSHW_6X200_NOTEXT
R1, R3, R5: 100k; R0805
R2, R4, R18: 10k; R0805
RESET: 31-XX; B3F-31XX
U$1, U$3, U$6: A4988BREAKOUT
U$2: DAC8552
U$9: M18_; 1X18
X1: MSTBA2
XY: 3PIN-HEADER

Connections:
+12V: C1.+, C2.1, C3.+, C4.+, C5.+, D1.A, D2.C, F1.1, U$1.VMOT, U$3.VMOT, U$6.VMOT
A-DIR: ARDUINO_DUE1.28, U$6.DIR
A-EN: ARDUINO_DUE1.24, R18.2, U$6.EN
A-STEP: ARDUINO_DUE1.26, U$6.STEP
AM-VIN: ARDUINO_DUE1.VIN, D1.C
B-DIR: ARDUINO_DUE1.34, U$1.DIR
B-EN: ARDUINO_DUE1.30, R2.2, U$1.EN
B-STEP: ARDUINO_DUE1.32, U$1.STEP
C-DIR: ARDUINO_DUE1.40, U$3.DIR
C-EN: ARDUINO_DUE1.36, R4.2, U$3.EN
C-STEP: ARDUINO_DUE1.38, U$3.STEP
D17: ARDUINO_DUE1.17 (RX2_17), U$9.17
D18: ARDUINO_DUE1.18 (TX1_18), U$9.18
D23: ARDUINO_DUE1.23, U$9.16
D25: ARDUINO_DUE1.25, U$9.15
D27: ARDUINO_DUE1.27, U$9.14
D29: ARDUINO_DUE1.29, U$9.13
D31: ARDUINO_DUE1.31, U$9.12
D32: U$9.3
D33: ARDUINO_DUE1.33, U$9.11
D35: ARDUINO_DUE1.35, U$9.10
D37: ARDUINO_DUE1.37, U$9.9
D39: ARDUINO_DUE1.39, U$9.8
D41: ARDUINO_DUE1.41, U$9.7
D43: ARDUINO_DUE1.43, U$9.6
D45: ARDUINO_DUE1.45, U$9.5
D47: ARDUINO_DUE1.47, U$9.4
DAC-VCC: ARDUINO_DUE1.5V_2 (5V_SPI), U$2.1 (VIN)
GND: ARDUINO_DUE1.GND, ARDUINO_DUE1.GND_1 (GND), ARDUINO_DUE1.GND_3 (GND), ARDUINO_DUE1.GND_5 (GND), C1.-, C2.2, C3.-, C4.-, C5.-, D2.A, R1.2, R3.2, R5.2, RESET.1, U$1.GND, U$1.GND@0 (GND), U$2.8 (GND), U$3.GND, U$3.GND@0 (GND), U$6.GND, U$6.GND@0 (GND), U$9.2, X1.2, XY.2
MOSI: ARDUINO_DUE1.MOSI, U$2.7 (DIN)
unnamed: U$6.RST, U$6.SLP (SLEEP)
unnamed: F1.2, X1.1
unnamed: JP2.5, U$1.MS3
unnamed: JP2.1, R1.1, U$1.MS1
unnamed: JP2.3, U$1.MS2
unnamed: B-MOT.1, U$1.2B
unnamed: B-MOT.2, U$1.2A
unnamed: B-MOT.3, U$1.1A
unnamed: B-MOT.4, U$1.1B
unnamed: U$1.RST, U$1.SLP (SLEEP)
unnamed: JP3.5, U$3.MS3
unnamed: U$2.3 (B), XY.3
unnamed: U$2.4 (A), XY.1
unnamed: JP1.1, R5.1, U$6.MS1
unnamed: JP1.3, U$6.MS2
unnamed: JP3.1, R3.1, U$3.MS1
unnamed: JP3.3, U$3.MS2
unnamed: C-MOT.1, U$3.2B
unnamed: JP1.5, U$6.MS3
unnamed: C-MOT.2, U$3.2A
unnamed: A-MOT.1, U$6.2B
unnamed: A-MOT.2, U$6.2A
unnamed: C-MOT.3, U$3.1A
unnamed: C-MOT.4, U$3.1B
unnamed: U$3.RST, U$3.SLP (SLEEP)
unnamed: A-MOT.3, U$6.1A
unnamed: A-MOT.4, U$6.1B
RESET: ARDUINO_DUE1.RESET, RESET.2 (S)
SCLK: ARDUINO_DUE1.SPCK, U$2.6 (SCLK)
SN: ARDUINO_DUE1.16 (TX2_16), U$2.5 (SN)
VCC: ARDUINO_DUE1.5V0 (5V), JP1.2, JP1.4, JP1.6, JP2.2, JP2.4, JP2.6, JP3.2, JP3.4, JP3.6, R2.1, R4.1, R18.1, U$1.VDD, U$3.VDD, U$6.VDD, U$9.1
Z-MIN: ARDUINO_DUE1.15 (RX3_15)

Board: 2 copper layers, 30 parts (0 on the bottom side), 60 nets, no tracks yet.

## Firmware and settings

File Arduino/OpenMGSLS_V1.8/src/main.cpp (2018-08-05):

/*
 Name:		OpenMGSLS.ino
 Created:	2018/1/6 21:51:00
 Author:	QiayuanLiao
 Version:	1.8
*/
#include <Arduino.h>
#include <SPI.h>
#include "XYMG.h"
#include "Planner.h"
#include "Command.h"
#include "Stepper.h"
#include "Heating.h"
// the setup function runs once when you press reset or power the board
void setup() {
	Init_Command();
	Init_XYMG();
	Init_Stepper();
//	Init_Heating();
}
// the loop function runs over and over again until power down or reset
void loop() {
	if (GCodeBuffLen_int_Command < (GCODE_BUFF_SIZE - 1)) {
		Get_Command();
	}
	if (GCodeBuffLen_int_Command && (DAValBufferLen_int_Planner < (DA_VAL_BUFF_SIZE - 1))) {
		Process_Command();
		if (NeedMove_boolArry_Command[0]) {
			NeedMove_boolArry_Command[0] = false;
			NeedOpenLaser_boolArry_Planner[DAValBufferPlanCouter_int_Planner] = NeedMove_boolArry_Command[1];
			NeedMove_boolArry_Command[1] = false;
			PlaneXY_Planner();
		}
		else if (NeedMove_boolArry_Command[2]) {
			NeedMove_boolArry_Command[2] = false;
			if (abs(GCodeVal_floatArry_Command[2] - Z_Position_Old) < 0.1)
				StepperB_StartMove(0.2);
			else
				StepperB_StartMove((GCodeVal_floatArry_Command[2] - Z_Position_Old)*1.5);
			while (IsMoving_B)
				delay(1);

			StepperC_StartMove(-(GCodeVal_floatArry_Command[2] - Z_Position_Old));
			while (IsMoving_C)
				delay(1);

			StepperA_StartMove(Stepper_A_DISTANCE_MAX);
			while (IsMoving_A)
				delay(1);

			StepperA_StartMove(-Stepper_A_DISTANCE_MAX);
			while (IsMoving_A)
				delay(1);

			Z_Position_Old = GCodeVal_floatArry_Command[2];
		}
		else if (NeedMove_boolArry_Command[3]) {
			NeedMove_boolArry_Command[3] = false;

			StepperA_StartMove(Stepper_A_DISTANCE_MAX);
			while (IsMoving_A)
				delay(1);
			StepperA_StartMove(-Stepper_A_DISTANCE_MAX);
			while (IsMoving_A)
				delay(1);
		}
		else if (NeedMove_boolArry_Command[4]) {
			NeedMove_boolArry_Command[4] = false;
			StepperB_StartMove(GCodeVal_floatArry_Command[4]);
			while (IsMoving_B)
				delay(1);
		}
		else if (NeedMove_boolArry_Command[5]) {
			NeedMove_boolArry_Command[5] = false;
			StepperC_StartMove(GCodeVal_floatArry_Command[5]);
			while (IsMoving_C)
				delay(1);
		}

	}
	if (DAValBufferLen_int_Planner && !IsMoving_XY) {
		DAValMoveX_ushortPointer_XYMG = DAValBufferX_ushortPointer_Planner[DAValBufferMoveCouter_int_Planner];
		DAValMoveY_ushortPointer_XYMG = DAValBufferY_ushortPointer_Planner[DAValBufferMoveCouter_int_Planner];
		NeedOpenLaser_bool_XYMG = NeedOpenLaser_boolArry_Planner[DAValBufferMoveCouter_int_Planner];
		Times_LinearLnterpolation_int_XYMG = Times_LinearLnterpolation_intArry_Planner[DAValBufferMoveCouter_int_Planner];
		XYMG_StartMove();
		DAValBufferMoveCouter_int_Planner = (DAValBufferMoveCouter_int_Planner + 1) % DA_VAL_BUFF_SIZE;
		DAValBufferLen_int_Planner--;
	}
}

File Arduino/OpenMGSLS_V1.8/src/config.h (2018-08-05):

//Command
#define MYSERIAL Serial
#define SPEED_SERIAL 250000
#define GCODE_BUFF_SIZE 3
//XYMG

#define SPEED_SPI 50000000
#define BASE_VOLTAGE 4.8//
#define LASER_OFF_POWER 10//0-255  correspond 0-5W (when the laser max power is 5W)
#define LASER_ON_POWER 255
#define PIN_XY 16
#define PIN_LASER 32
//Stepper
#define STEPPER_A_STEP_PER_UNIT 13.3333
#define STEPPER_A_ACCELERATION 300
#define STEPPER_A_TIMER Timer4
#define STEPPER_A_SPEED 250
#define STEPPER_A_PIN_EN 24
#define STEPPER_A_PIN_STEP 47
#define STEPPER_A_PIN_DIR 45
#define STEPPER_A_NEGATE false

#define STEPPER_B_STEP_PER_UNIT 200
#define STEPPER_B_ACCELERATION 100
#define STEPPER_B_TIMER Timer4
#define STEPPER_B_SPEED 50
#define STEPPER_B_PIN_EN 0
#define STEPPER_B_PIN_STEP 43
#define STEPPER_B_PIN_DIR 41
#define STEPPER_B_NEGATE true


#define STEPPER_C_STEP_PER_UNIT 200
#define STEPPER_C_ACCELERATION 100
#define STEPPER_C_TIMER Timer4
#define STEPPER_C_SPEED 50
#define STEPPER_C_PIN_EN 0
#define STEPPER_C_PIN_STEP 39
#define STEPPER_C_PIN_DIR 37
#define STEPPER_C_NEGATE true

#define Stepper_A_DISTANCE_MAX 400

//Planner
#define DA_VAL_BUFF_SIZE 3
#define DA_VAL_ARRY_SIZE 6000
#define SPEED_XY 3000 //  mm per seconds
#define DIS_F_THETA 260//distance between F-Theta and plane
#define DIS_XYMOTOR 8
#define RAD_MG_MAX 0.349065 //the Mirror galvanometer max rad  (20/180*pi)
#define CYCLE_LNTERPOLARION 3000// per seconds

//heating
#define HEATING_PIN 35
#define HEATING_CYCLE 4000000 //mirosecond
#define HEATING_PROPORTION 0.43
#define HEATING_TIMER Timer6

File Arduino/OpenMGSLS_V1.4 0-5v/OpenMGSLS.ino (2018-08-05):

/*
 Name:		OpenMGSLS.ino
 Created:	2017/1/16 23:09:56
 Author:	liaoq
 Version:	1.4
*/

// the setup function runs once when you press reset or power the board
#include <SPI.h>
#include "XYMG.h"
#include "Planter.h"
#include "Command.h"

void setup() {
	Command_Init();
	XYMG_Init();
}
// the loop function runs over and over again until power down or reset
void loop() {
	Command_Get();
	if (NeedPlane_XY_bool_Command) {
		Plane_XY(GCode_Arry_Command);
		NeedPlane_XY_bool_Command = false;
		if (NeedMove_XY_bool_Command)
			XYMG_StartMove();
		NeedMove_XY_bool_Command = false;
	}
	while (1) {
		delay(1);
		if (!IsMoving)
			break;
	}
}

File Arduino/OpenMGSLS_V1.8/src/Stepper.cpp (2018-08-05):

// 
// 
// 
//this part of control theory is base on : 
//http://hwml.com/LeibRamp.pdf

#include "Stepper.h"
float Stepper_Multiplier[3];
float Stepper_Delay_Period[3];

int Stepper_Distance_Goal_Step[3];
int Stepper_Distance_Now_Step[3];
int Stepper_Distance_Acceleration_Step[3];

float Z_Position_Old;

bool IsMoving_A;
bool IsMoving_B;
bool IsMoving_C;

int Stepper_Acceleration_Step[3] = {
	STEPPER_A_ACCELERATION*STEPPER_A_STEP_PER_UNIT,
	STEPPER_B_ACCELERATION*STEPPER_B_STEP_PER_UNIT,
	STEPPER_C_ACCELERATION*STEPPER_C_STEP_PER_UNIT,
};

int Stepper_Speed_Step[3]{
	STEPPER_A_SPEED*STEPPER_A_STEP_PER_UNIT,
	STEPPER_B_SPEED*STEPPER_B_STEP_PER_UNIT,
	STEPPER_C_SPEED*STEPPER_C_STEP_PER_UNIT,
};

void Init_Stepper() {
	pinMode(STEPPER_A_PIN_STEP, OUTPUT);
	pinMode(STEPPER_B_PIN_STEP, OUTPUT);
	pinMode(STEPPER_C_PIN_STEP, OUTPUT);
	pinMode(STEPPER_A_PIN_DIR, OUTPUT);
	pinMode(STEPPER_B_PIN_DIR, OUTPUT);
	pinMode(STEPPER_C_PIN_DIR, OUTPUT);
	Stepper_Distance_Acceleration_Step[0] = Stepper_Speed_Step[0] * Stepper_Speed_Step[0] / (2 * Stepper_Acceleration_Step[0]);
	Stepper_Multiplier[0] = Stepper_Acceleration_Step[0] / 1000000.0 / 1000000.0;
	Stepper_Distance_Acceleration_Step[1] = Stepper_Speed_Step[1] * Stepper_Speed_Step[1] / (2 * Stepper_Acceleration_Step[1]);
	Stepper_Multiplier[1] = Stepper_Acceleration_Step[1] / 1000000.0 / 1000000.0;
	Stepper_Distance_Acceleration_Step[2] = Stepper_Speed_Step[2] * Stepper_Speed_Step[2] / (2 * Stepper_Acceleration_Step[2]);
	Stepper_Multiplier[2] = Stepper_Acceleration_Step[2] / 1000000.0 / 1000000.0;
}
void StepperA_StartMove(float dis) {

	Stepper_Distance_Goal_Step[0] = dis*STEPPER_A_STEP_PER_UNIT;

	if (Stepper_Distance_Goal_Step[0] > 0)
		digitalWrite(STEPPER_A_PIN_DIR, STEPPER_A_NEGATE);

	else
		digitalWrite(STEPPER_A_PIN_DIR, !STEPPER_A_NEGATE);

	Stepper_Distance_Goal_Step[0] = abs(Stepper_Distance_Goal_Step[0]);

	if (Stepper_Distance_Acceleration_Step[0] > Stepper_Distance_Goal_Step[0] / 2)
		Stepper_Distance_Acceleration_Step[0] = Stepper_Distance_Goal_Step[0] / 2;

	Stepper_Delay_Period[0] = 1000000.0 / sqrtf(2 * Stepper_Acceleration_Step[0]);
	IsMoving_A = true;
	STEPPER_A_TIMER.attachInterrupt(StepperA_Moving).setPeriod(Stepper_Delay_Period[0]).start();

}
void StepperA_Moving() {
		if (Stepper_Distance_Now_Step[0] < Stepper_Distance_Goal_Step[0]) {
		Stepper_Distance_Now_Step[0]++;
		digitalWrite(STEPPER_A_PIN_STEP, HIGH);
		
		if (Stepper_Distance_Now_Step[0] >= Stepper_Distance_Goal_Step[0] - Stepper_Distance_Acceleration_Step[0])
			Stepper_Delay_Period[0] = Stepper_Delay_Period[0] * (1 + Stepper_Multiplier[0] * Stepper_Delay_Period[0] * Stepper_Delay_Period[0]);
		else if (Stepper_Distance_Now_Step[0] < Stepper_Distance_Acceleration_Step[0])
			Stepper_Delay_Period[0] = Stepper_Delay_Period[0] * (1 - Stepper_Multiplier[0] * Stepper_Delay_Period[0] * Stepper_Delay_Period[0]);
		
		digitalWrite(STEPPER_A_PIN_STEP, LOW);
		STEPPER_A_TIMER.setPeriod(Stepper_Delay_Period[0]).start();
	}
	else {
		STEPPER_A_TIMER.stop();
		IsMoving_A = false;
		Stepper_Distance_Now_Step[0] = 0;
	}
}

void StepperB_StartMove(float dis) {

		Stepper_Distance_Goal_Step[1] = dis*STEPPER_B_STEP_PER_UNIT;
	if (Stepper_Distance_Goal_Step[1] > 0)
		digitalWrite(STEPPER_B_PIN_DIR, STEPPER_B_NEGATE);
	else
		digitalWrite(STEPPER_B_PIN_DIR, !STEPPER_B_NEGATE);

	Stepper_Distance_Goal_Step[1] = abs(Stepper_Distance_Goal_Step[1]);

	if (Stepper_Distance_Acceleration_Step[1] > Stepper_Distance_Goal_Step[1] / 2)
		Stepper_Distance_Acceleration_Step[1] = Stepper_Distance_Goal_Step[1] / 2;
	
	Stepper_Delay_Period[1] = 1000000.0 / sqrtf(2 * Stepper_Acceleration_Step[1]);
	IsMoving_B = true;
	STEPPER_B_TIMER.attachInterrupt(StepperB_Moving).setPeriod(Stepper_Delay_Period[1]).start();

}
void StepperB_Moving() {
	if (Stepper_Distance_Now_Step[1] < Stepper_Distance_Goal_Step[1]) {
		Stepper_Distance_Now_Step[1]++;
		digitalWrite(STEPPER_B_PIN_STEP, HIGH);

		if (Stepper_Distance_Now_Step[1] >= Stepper_Distance_Goal_Step[1] - Stepper_Distance_Acceleration_Step[1])
			Stepper_Delay_Period[1] = Stepper_Delay_Period[1] * (1 + Stepper_Multiplier[1] * Stepper_Delay_Period[1] * Stepper_Delay_Period[1]);
		else if (Stepper_Distance_Now_Step[1] < Stepper_Distance_Acceleration_Step[1])
			Stepper_Delay_Period[1] = Stepper_Delay_Period[1] * (1 - Stepper_Multiplier[1] * Stepper_Delay_Period[1] * Stepper_Delay_Period[1]);

		digitalWrite(STEPPER_B_PIN_STEP, LOW);
		STEPPER_B_TIMER.setPeriod(Stepper_Delay_Period[1]).start();
	}
	else {
		STEPPER_B_TIMER.stop();
		IsMoving_B = false;
		Stepper_Distance_Now_Step[1] = 0;
	}
}
void StepperC_StartMove(float dis) {

		Stepper_Distance_Goal_Step[2] = dis*STEPPER_C_STEP_PER_UNIT;

	if (Stepper_Distance_Goal_Step[2] > 0)
		digitalWrite(STEPPER_C_PIN_DIR, STEPPER_C_NEGATE);

	else
		digitalWrite(STEPPER_C_PIN_DIR, !STEPPER_C_NEGATE);

	Stepper_Distance_Goal_Step[2] = abs(Stepper_Distance_Goal_Step[2]);

	if (Stepper_Distance_Acceleration_Step[2] > Stepper_Distance_Goal_Step[2] / 2)
		Stepper_Distance_Acceleration_Step[2] = Stepper_Distance_Goal_Step[2] / 2;

	Stepper_Delay_Period[2] = 1000000.0 / sqrtf(2 * Stepper_Acceleration_Step[2]);
	IsMoving_C = true;
	STEPPER_C_TIMER.attachInterrupt(StepperC_Moving).setPeriod(Stepper_Delay_Period[2]).start();

}
void StepperC_Moving() {
	if (Stepper_Distance_Now_Step[2] < Stepper_Distance_Goal_Step[2]) {
		Stepper_Distance_Now_Step[2]++;
		digitalWrite(STEPPER_C_PIN_STEP, HIGH);

		if (Stepper_Distance_Now_Step[2] >= Stepper_Distance_Goal_Step[2] - Stepper_Distance_Acceleration_Step[2])
			Stepper_Delay_Period[2] = Stepper_Delay_Period[2] * (1 + Stepper_Multiplier[2] * Stepper_Delay_Period[2] * Stepper_Delay_Period[2]);
		else if (Stepper_Distance_Now_Step[2] < Stepper_Distance_Acceleration_Step[2])
			Stepper_Delay_Period[2] = Stepper_Delay_Period[2] * (1 - Stepper_Multiplier[2] * Stepper_Delay_Period[2] * Stepper_Delay_Period[2]);

		digitalWrite(STEPPER_C_PIN_STEP, LOW);
		STEPPER_C_TIMER.setPeriod(Stepper_Delay_Period[2]).start();
	}
	else {
		STEPPER_C_TIMER.stop();
		IsMoving_C = false;
		Stepper_Distance_Now_Step[2] = 0;
	}
}

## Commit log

2018-08-05 add cad drawing file
    [0804.SLDPRT, 081640.SLDPRT, 082040.SLDPRT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]
2018-08-05 add arduino code
    [DAC8552_Dream.PcbLib, DAC8552_Dream.SchLib]
